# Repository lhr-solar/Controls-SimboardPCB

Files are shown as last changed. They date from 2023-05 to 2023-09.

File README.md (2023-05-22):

# Controls-SimboardPCB

Board's Purpose:

The Controls Sim Board interfaces with the Controls Leader Board in order to simulate the interfacing of the controls system on the car. 

Connections:

LEDs:
* Motor main contactor signal (D1)
* Motor precharge contactor signal (D2)
* Array main contactor signal (D3)
* Array precharge contactor signal  (D4)
Potentiometers:
* Accelerator
* Brake
Switches:
* Ignition
Other:
* CAN connections
* Controls Minion Board passthrough

Mouser BOM:
* Cart link: https://www.mouser.com/ProjectManager/ProjectDetail.aspx?AccessID=63b65d6ddb
* (Spreadsheet of BOM in repo as "Controls-Simboard MouserBom.xls")

Components Outside of Regular Volume:
* 538-43045-1412 (7x2 Molex connector)
* 538-43650-0415 (4x1 Molex connector)
* 538-43045-0612 (3x2 Molex connector)
* 10WA325 (Rotary switch)
* 179-TS16121295260STT (Push button)
* 652-PA45432015CPA503 (Slide Potentiometer)

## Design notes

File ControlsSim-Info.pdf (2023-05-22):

Controls Simboard PCB Information

Full Schematic

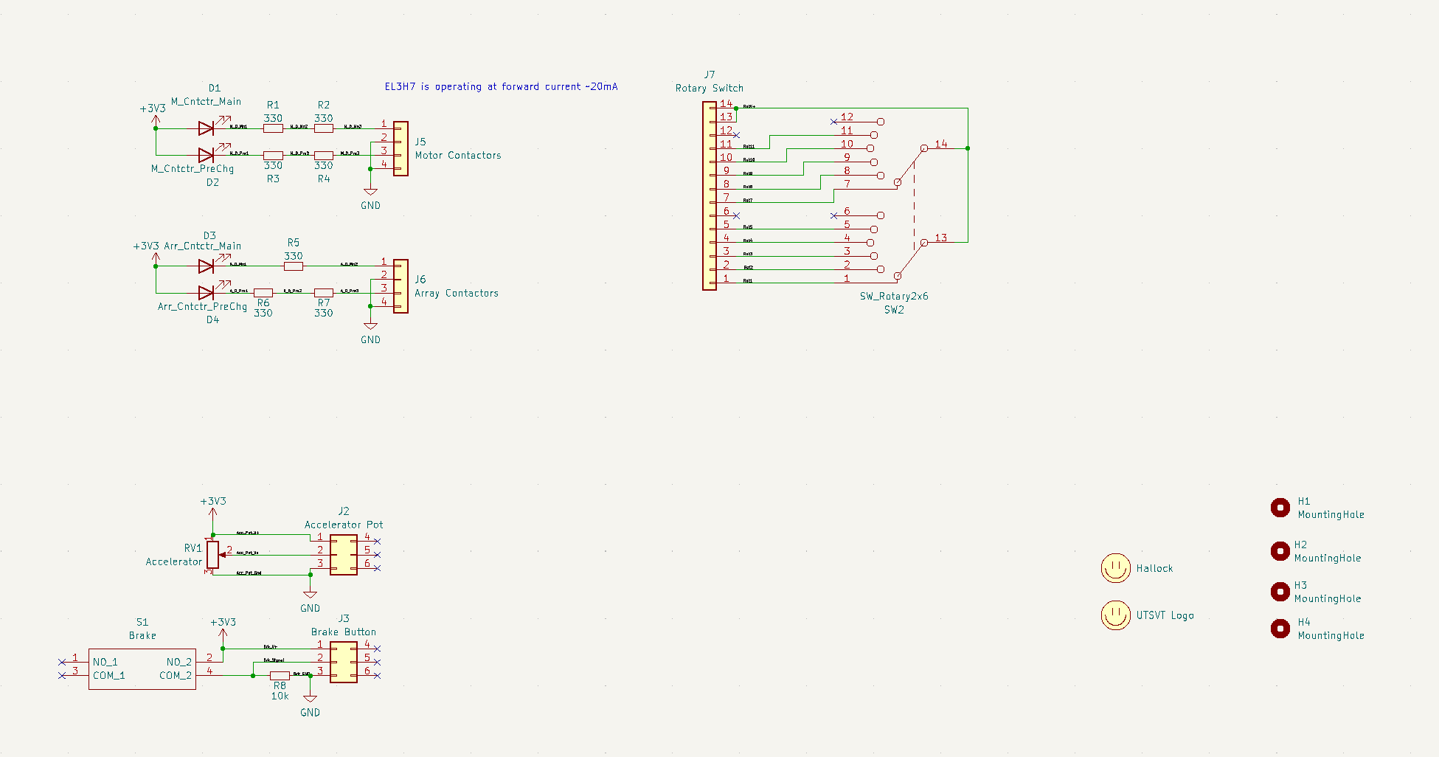
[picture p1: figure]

Board Layout

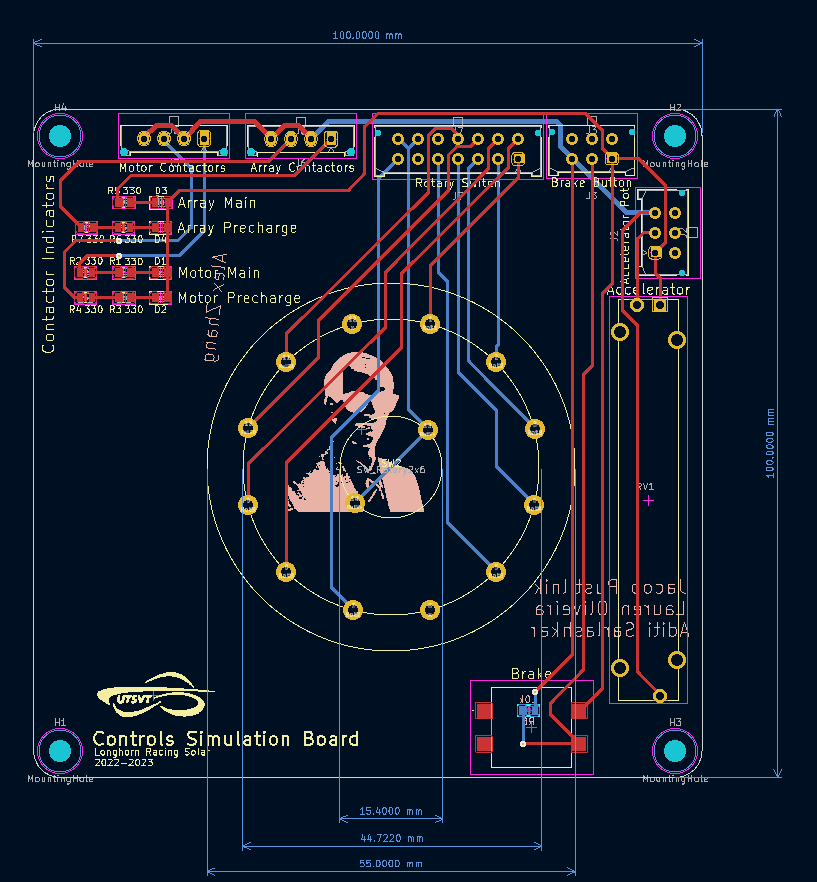
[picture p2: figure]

Board Layout 3D Front

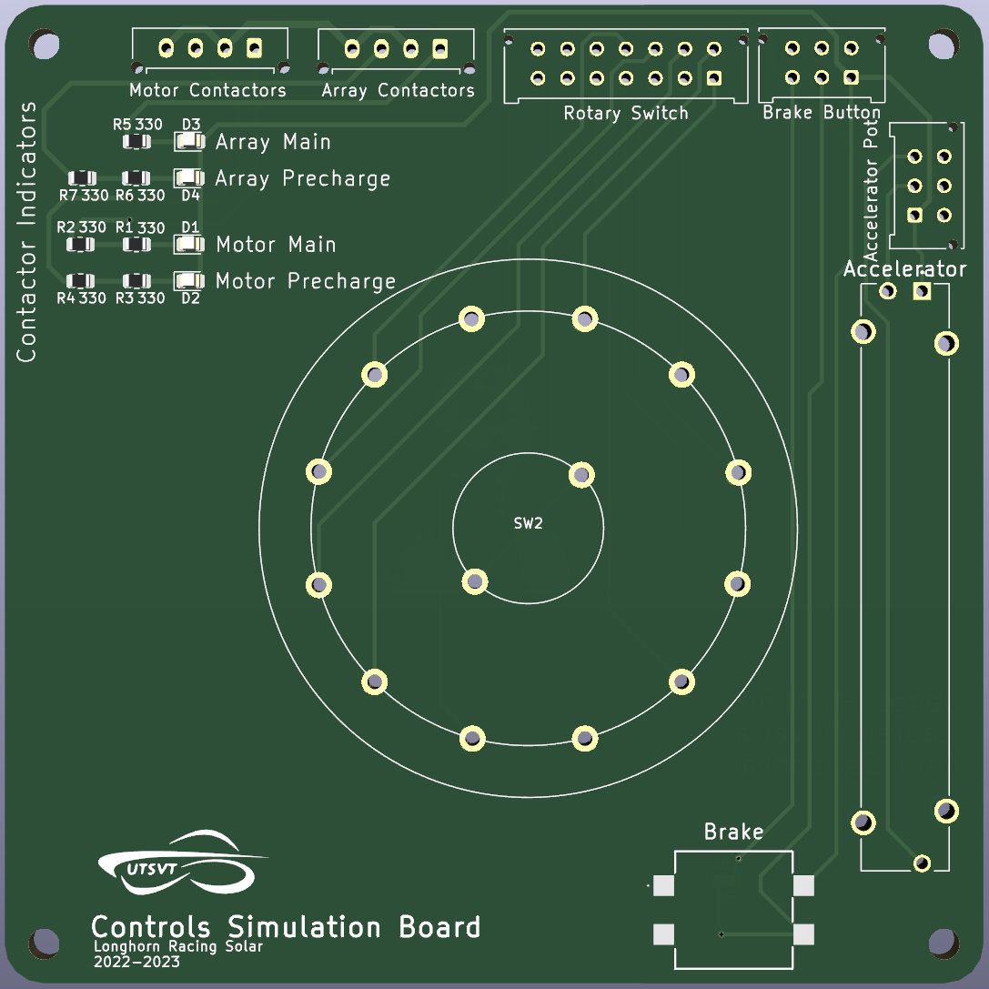
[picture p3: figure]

Board Layout 3D Back

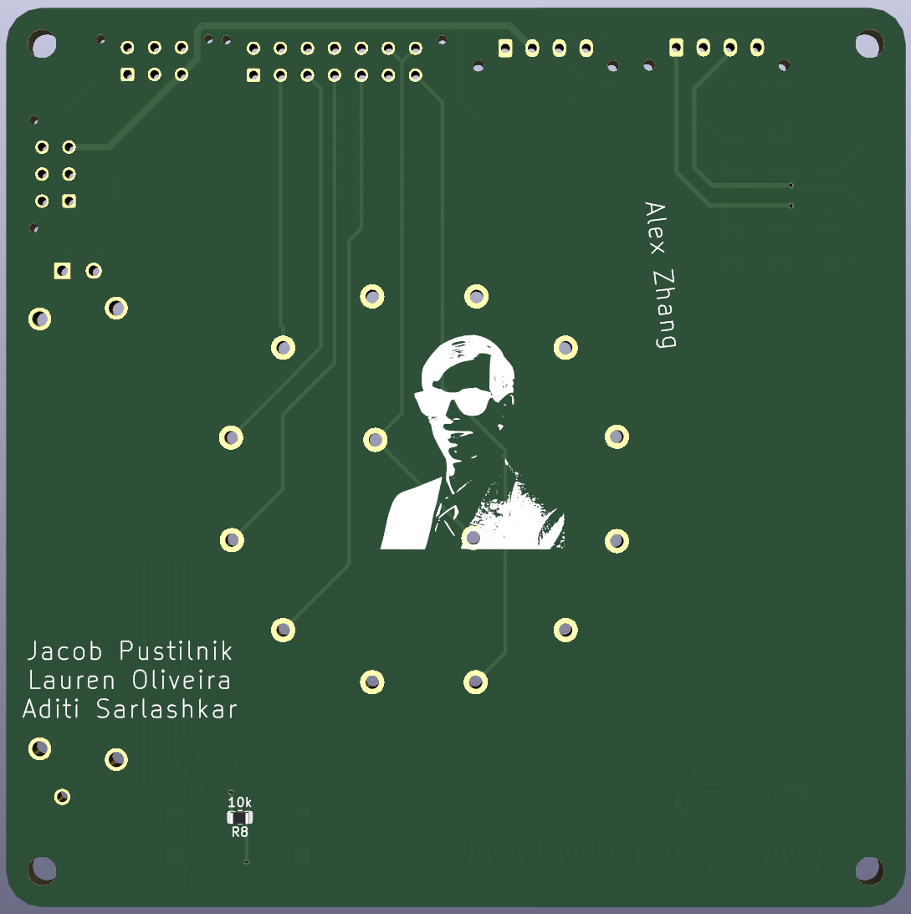
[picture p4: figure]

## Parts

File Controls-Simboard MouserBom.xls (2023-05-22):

Mfr Part Number (Input) | Quantity 1 | Mfr Part Number | Mouser Part Number | Manufacturer Name | Description | Unit Price 1 | Order Quantity | Order Unit Price | Min./Mult. | Availability | Lead Time in Days | Lead Time in Weeks | Lifecycle | NCNR | RoHS | Pb Free | Package Type | Package Quantity | Datasheet URL | Product Image | Design Risk
538-43045-1412 | 1 | 43045-1412 | 538-43045-1412 | Molex | Headers & Wire Housings Headers & Wire Housings 14 CKT VERT HEADER | $3.09 | 1 | $3.09 | 1\1 | 10,056 | 119 | 17 |  | No | Yes | No | TRAY | 936 | https://www.mouser.com/datasheet/2/276/0430451412_PCB_HEADERS-168210.pdf |  | Product has high popularity and is readily available.
10WA325 | 1 | CK1035 | 10WA325 | Lorlin | Rotary Switches Rotary Switches RTRY 2POL 6POS SLDR 6.35X38MM FLAT SHAFT | $7.12 | 1 | $7.12 | 1\1 | 79 | 95 | 14 |  | No | Yes | No | TRAY | 50 | https://www.mouser.com/datasheet/2/242/CK_Datasheet_Mar_2020-1890608.pdf |  | Product has high popularity and is readily available.
538-43650-0415 | 2 | 43650-0415 | 538-43650-0415 | Molex | Headers & Wire Housings Headers & Wire Housings VERT SMT PCB HDR 4P sngl polarizing pins | $1.19 | 2 | $1.19 | 1\1 | 18,797 | 77 | 11 |  | No | Yes | Yes | TRAY | 120 | https://www.mouser.com/datasheet/2/276/0436500415_PCB_HEADERS-148705.pdf |  | Product has high popularity and is readily available.
538-43045-0612 | 2 | 43045-0612 | 538-43045-0612 | Molex | Headers & Wire Housings Headers & Wire Housings 6 CKT VERT HEADER | $0.67 | 2 | $0.67 | 1\1 | 12,341 | 119 | 17 |  | No | Yes | No | TRAY | 144 | https://www.mouser.com/datasheet/2/276/3/0430450612_PCB_HEADERS-2877224.pdf |  | Product has high popularity and is readily available.
179-TS16121295260STT | 1 | TS16-1212-95-BK-260-SMT-TR | 179-TS16121295260STT | CUI Devices | Tactile Switches Tactile Switches 12 x 12 mm 9.5 mm Actuactor Height 260gf Black Surface Mount TR SPST | $0.38 | 1 | $0.38 | 1\1 | 1,877 | 21 | 3 | New Product | No | Yes | No |  | 400 | https://www.mouser.com/datasheet/2/670/ts16-2944012.pdf |  | Product is new and is readily available.
71-CRCW080510K0FKEAC | 1 | CRCW080510K0FKEAC | 71-CRCW080510K0FKEAC | Vishay | Thick Film Resistors - SMD Thick Film Resistors - SMD 1/8Watt 10Kohms 1% Commercial Use | $0.10 | 1 | $0.10 | 1\1 | 1,149,420 | 191 | 28 |  | No | Yes | No | REEL | 5,000 | https://www.vishay.com/doc?28773 |  | Product has high popularity and is readily available.
71-CRCW0805330RJNEAC | 7 | CRCW0805330RJNEAC | 71-CRCW0805330RJNEAC | Vishay | Thick Film Resistors - SMD Thick Film Resistors - SMD 1/8Watt 330ohms 5% Commercial Use | $0.10 | 7 | $0.10 | 1\1 | 60,251 | 174 | 25 |  | No | Yes | No | REEL | 5,000 | https://www.vishay.com/doc?28773 |  | Product has high popularity and is readily available.
604-APTD2012LCGCK | 4 | APTD2012LCGCK | 604-APTD2012LCGCK | Kingbright | Standard LEDs - SMD Standard LEDs - SMD 0805 Dome Lens LED Green- 570nm | $0.40 | 4 | $0.40 | 1\1 | 36,893 | 56 | 8 |  | No | Yes | Yes | REEL | 3,000 | https://www.mouser.com/datasheet/2/216/APTD2012LCGCK-1102037.pdf |  | Product has high popularity and is readily available.
652-PA45432015CPA503 | 1 | PTA4543-2015CPA503 | 652-PA45432015CPA503 | Bourns | Slide Potentiometers Slide Potentiometers PANEL CONTROL - SLIDE CARBON | $2.07 | 1 | $2.07 | 1\1 | 490 | 140 | 20 |  | No | Yes | No | TRAY | 100 | https://www.mouser.com/datasheet/2/54/pta-778345.pdf |  | Product has high popularity and is readily available.

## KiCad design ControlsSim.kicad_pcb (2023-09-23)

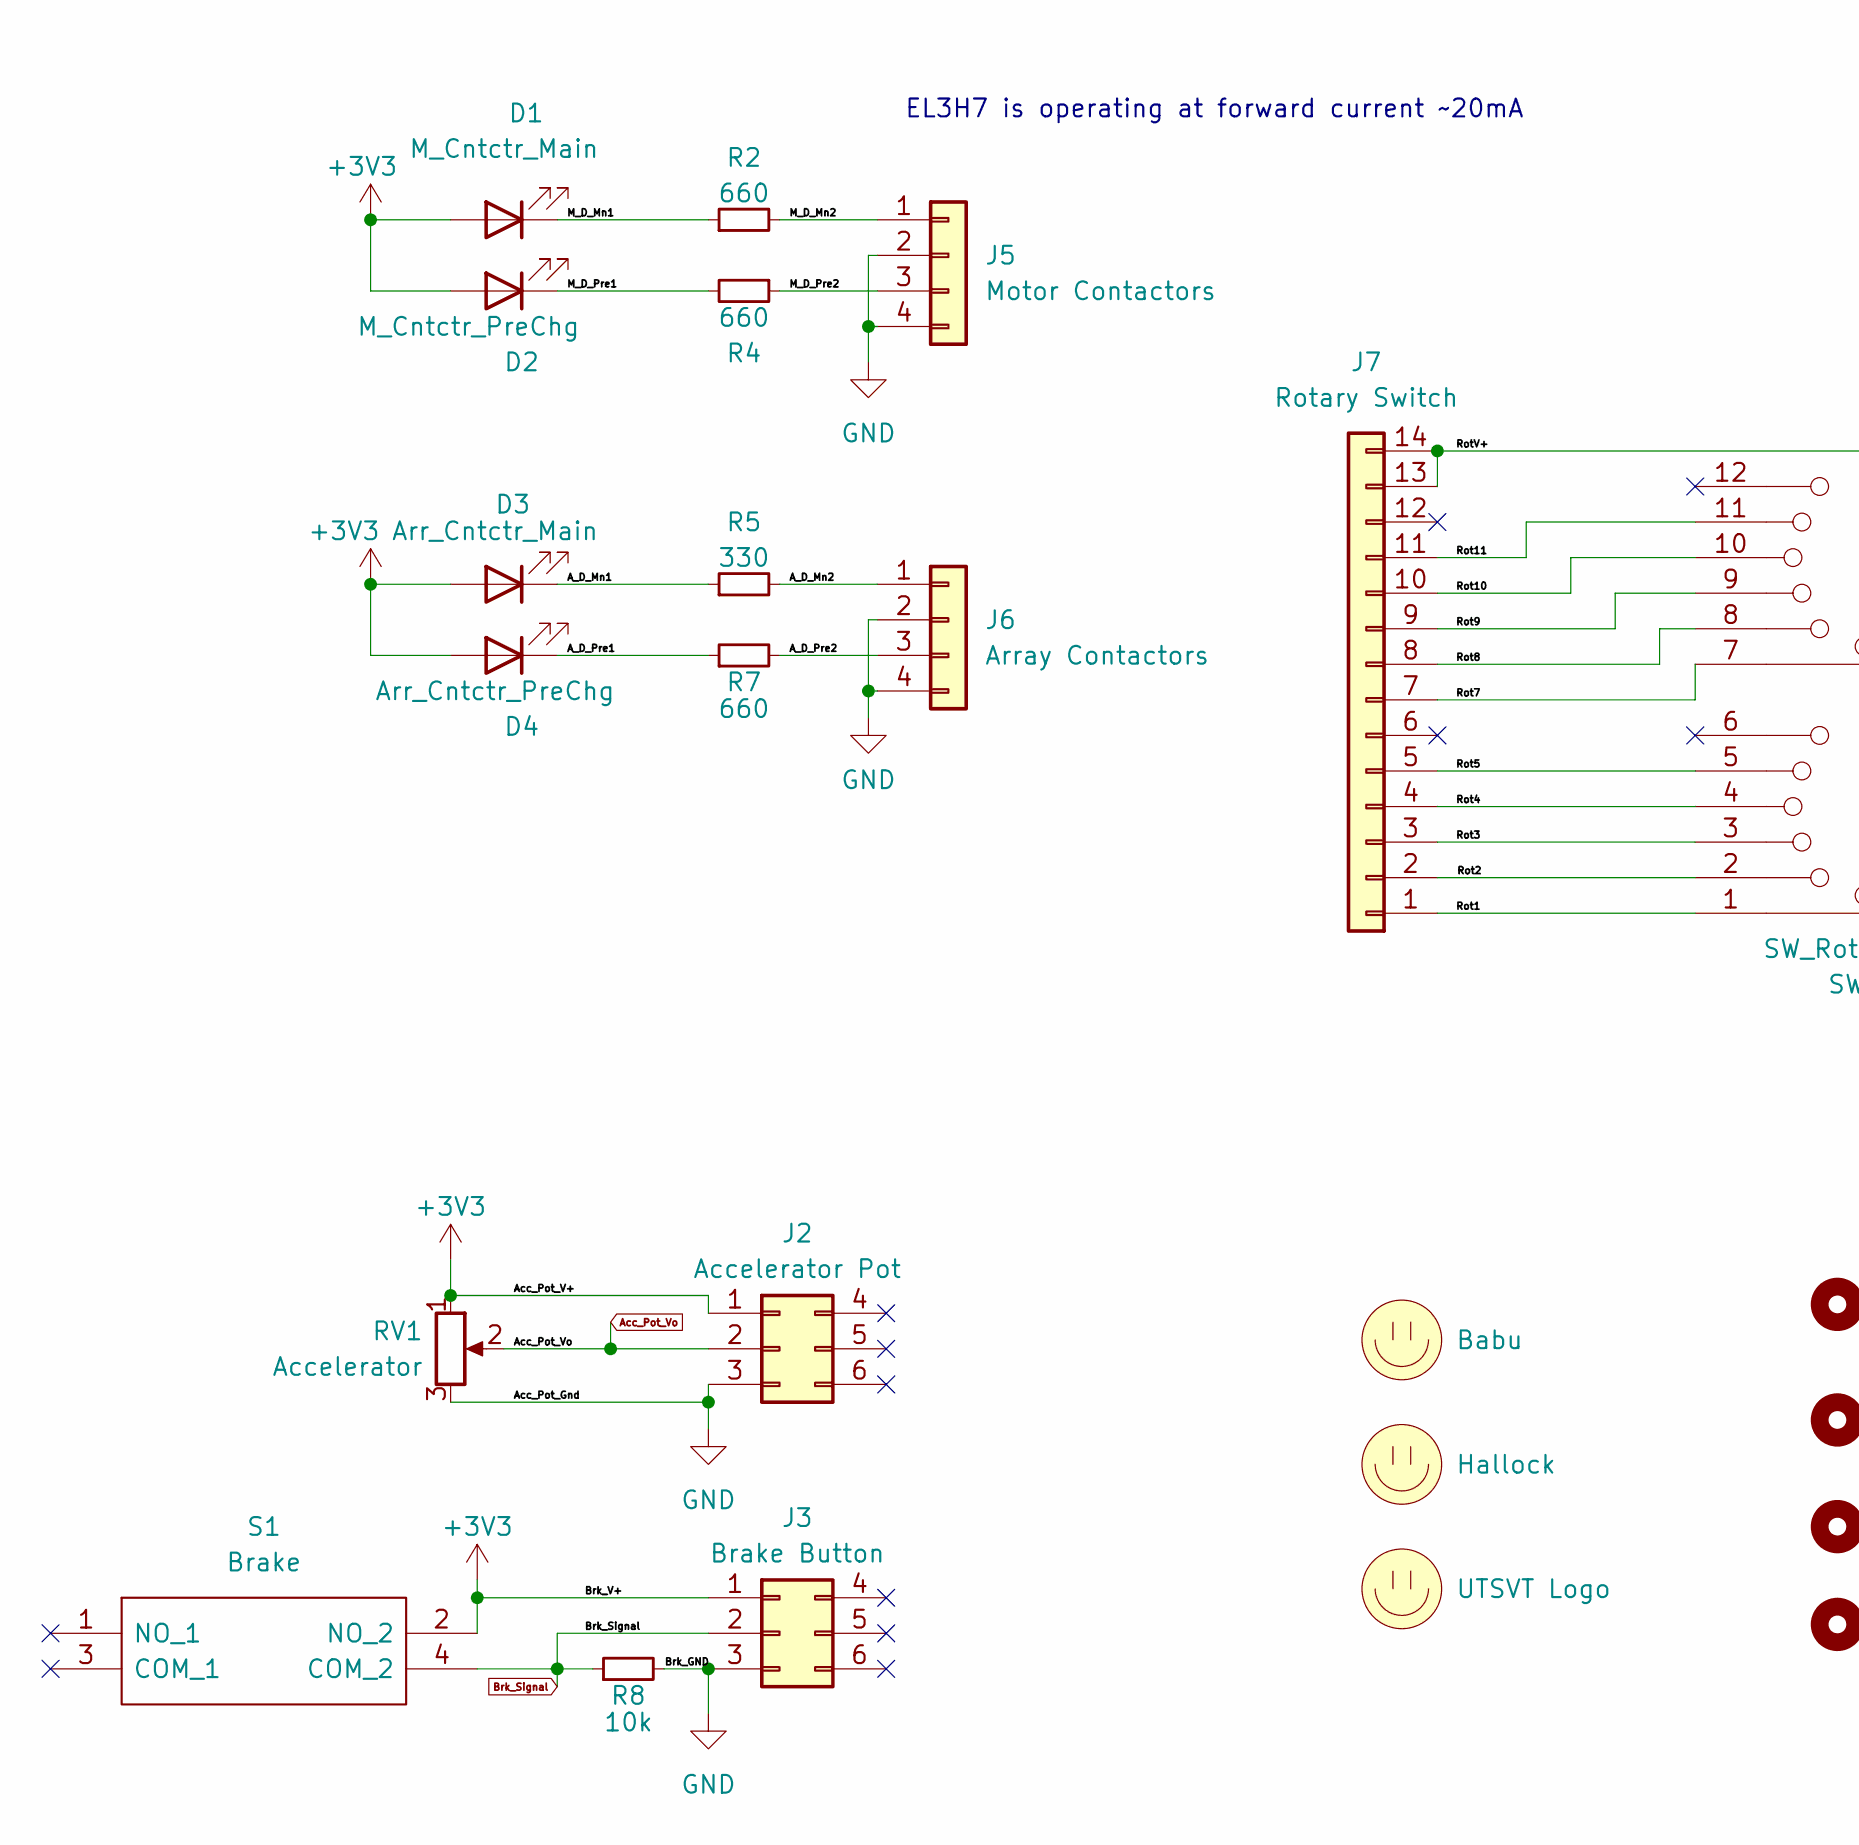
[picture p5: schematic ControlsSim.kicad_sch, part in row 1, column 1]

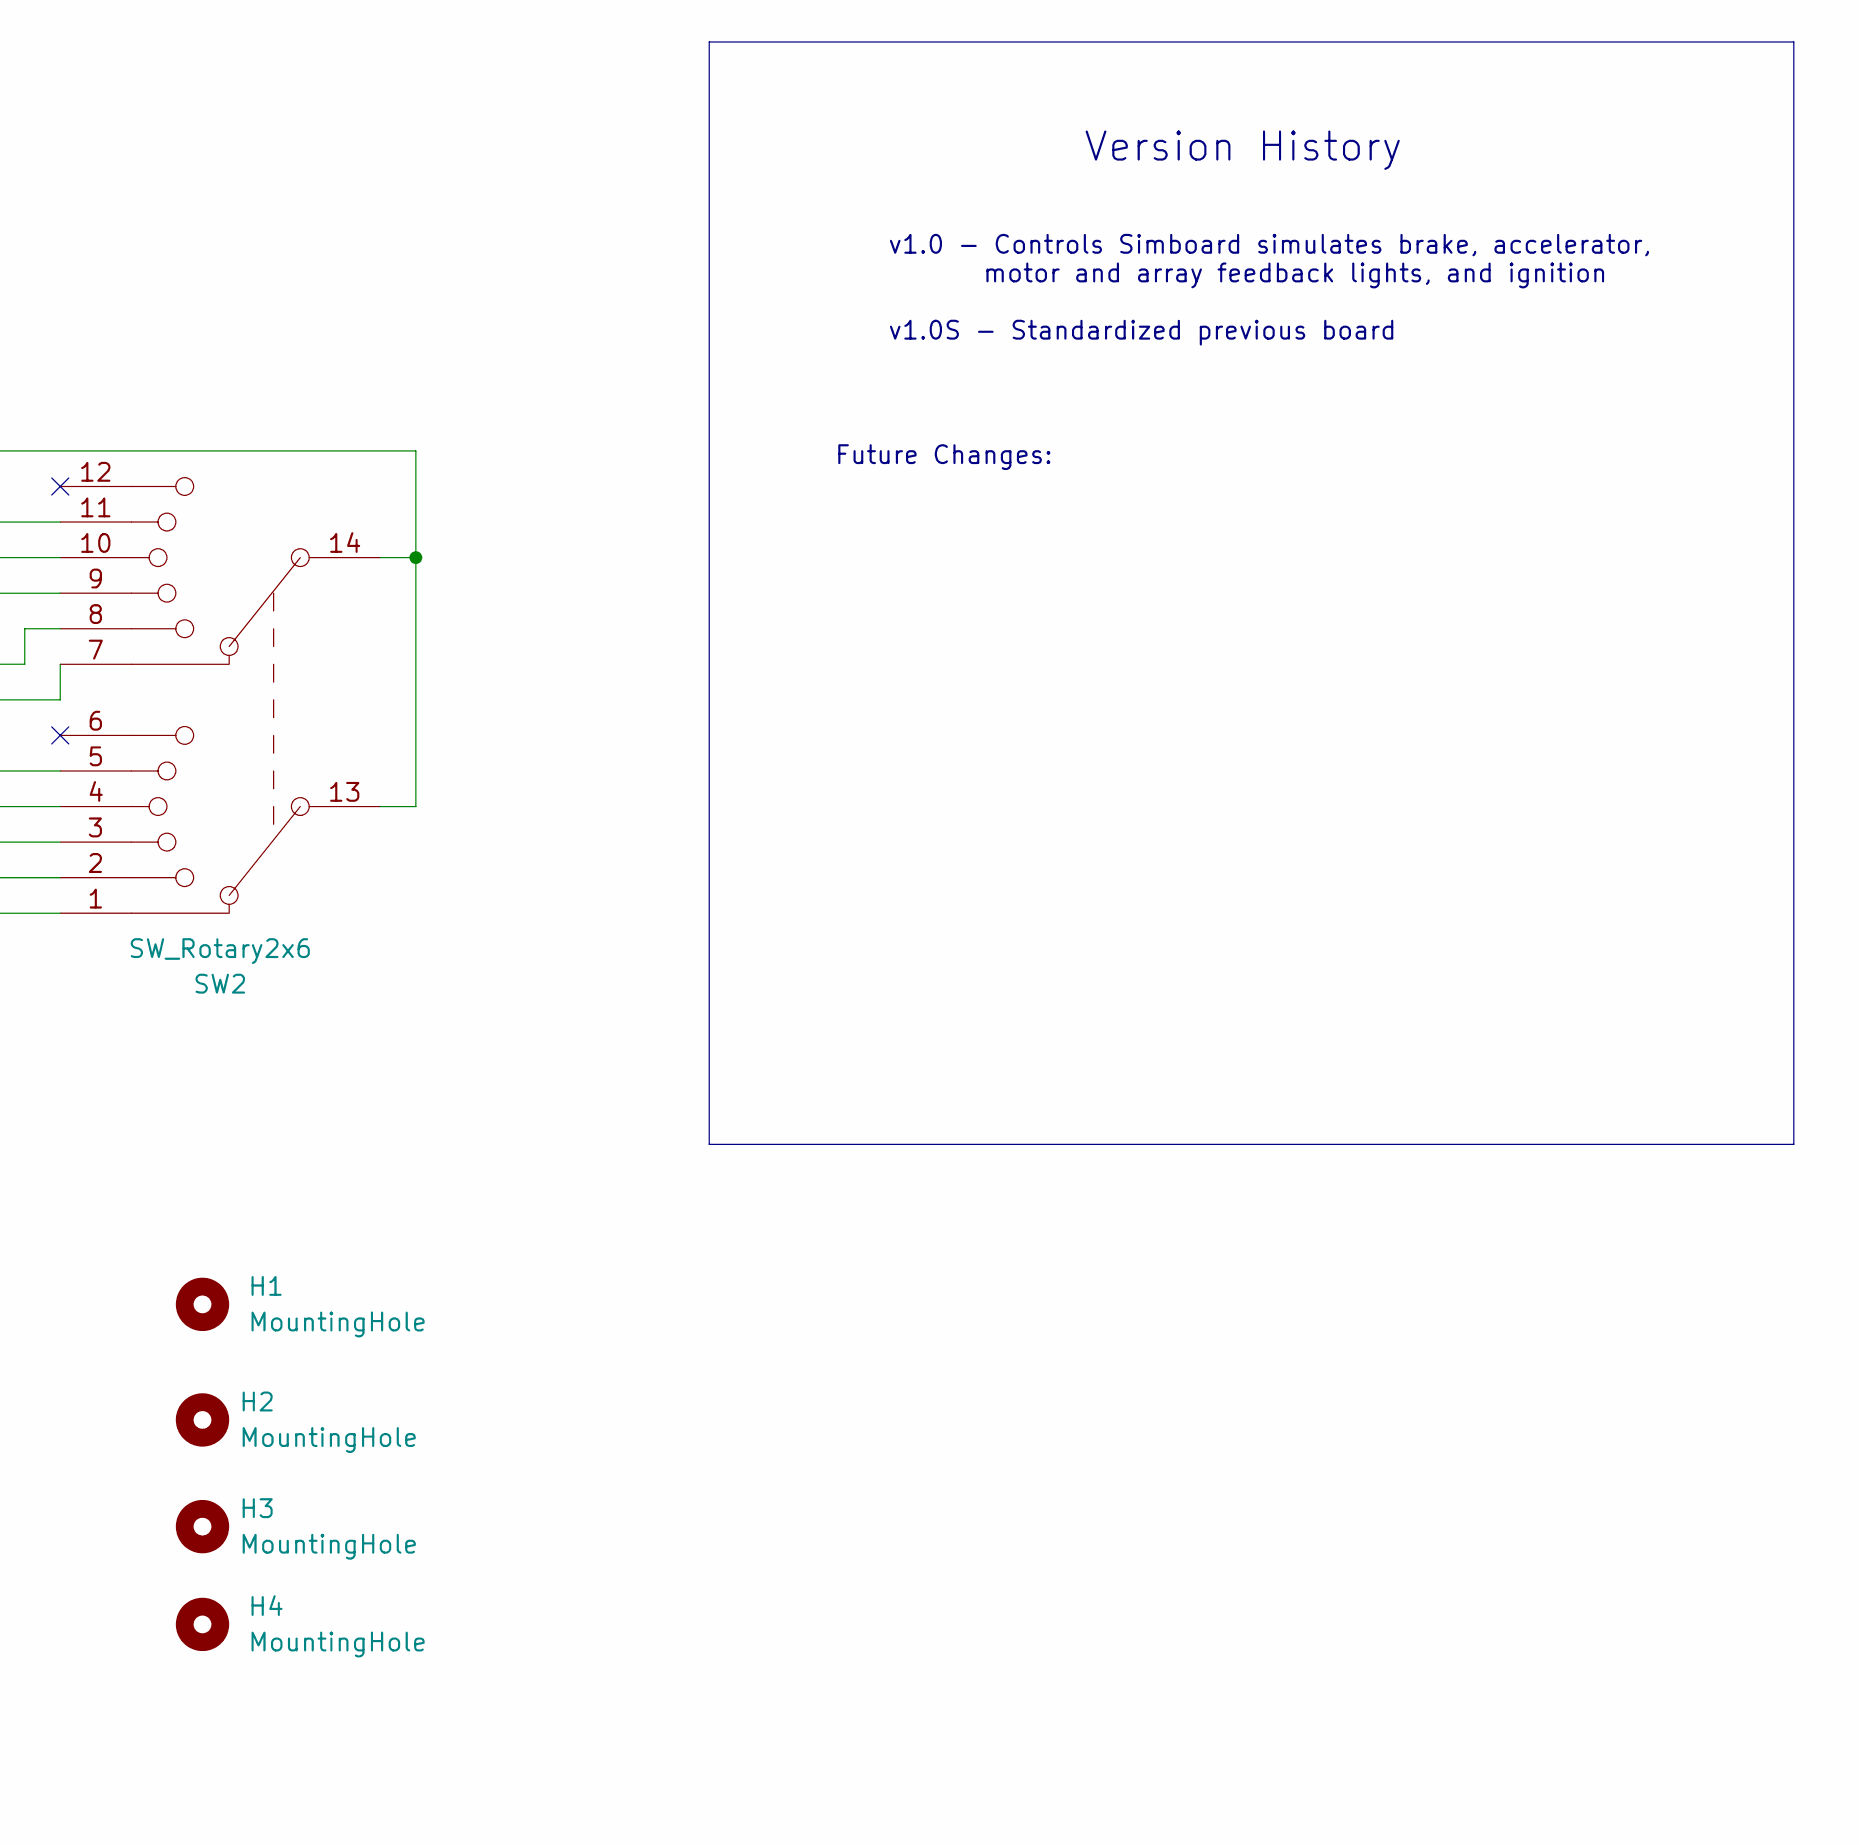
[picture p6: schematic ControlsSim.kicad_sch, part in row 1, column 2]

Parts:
D1: M_Cntctr_Main; LED_0805_2012Metric; MFG PN APTD2012LSYCK
D2: M_Cntctr_PreChg; LED_0805_2012Metric; MFG PN APTD2012LSURCK
D3: Arr_Cntctr_Main; LED_0805_2012Metric; MFG PN APTD2012LVBC/D
D4: Arr_Cntctr_PreChg; LED_0805_2012Metric; MFG PN APTD2012LCGCK
H1, H2, H3, H4: MountingHole; MountingHole_3.2mm_M3
J2: Accelerator Pot; Molex_Micro-Fit_3.0_43045-0612_2x03_P3.00mm_Vertical
J3: Brake Button; Molex_Micro-Fit_3.0_43045-0612_2x03_P3.00mm_Vertical
J5: Motor Contactors; Molex_Micro-Fit_3.0_43650-0415_1x04_P3.00mm_Vertical
J6: Array Contactors; Molex_Micro-Fit_3.0_43650-0415_1x04_P3.00mm_Vertical
J7: Rotary Switch; Molex_Micro-Fit_3.0_43045-1412_2x07_P3.00mm_Vertical
LOGO1: Hallock; Hallock_Image_Small
LOGO2: UTSVT Logo; UTSVT_Logo_Symbol
LOGO3: Babu; Babu the Builder
R2, R4, R7: 660; R_0805_2012Metric
R5: 330; R_0805_2012Metric
R8: 10k; R_0805_2012Metric; Mfg PN CRCW080510K0FKEAC
RV1: Accelerator; PTA4543
S1: Brake; TS16121295BK260SMTTR; Manufacturer_Part_Number TS16-1212-95-BK-260-SMT-TR
SW2: SW_Rotary2x6; CK1035_resized

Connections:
+3V3: D1.2 (A), D2.2 (A), D3.2 (A), D4.2 (A), J2.1, J3.1, RV1.1, S1.2 (NO_2)
/A_D_Mn1: D3.1 (K), R5.1
/A_D_Mn2: J6.1, R5.2
/A_D_Pre1: D4.1 (K), R7.1
/A_D_Pre2: J6.3, R7.2
/M_D_Mn1: D1.1 (K), R2.1
/M_D_Mn2: J5.1, R2.2
/M_D_Pre1: D2.1 (K), R4.2
/M_D_Pre2: J5.3, R4.1
/Rot1: J7.1, SW2.1
/Rot2: J7.2, SW2.2
/Rot3: J7.3, SW2.3
/Rot4: J7.4, SW2.4
/Rot5: J7.5, SW2.5
/Rot7: J7.7, SW2.7
/Rot8: J7.8, SW2.8
/Rot9: J7.9, SW2.9
/Rot10: J7.10, SW2.10
/Rot11: J7.11, SW2.11
/RotV+: J7.13, J7.14, SW2.13, SW2.14
Acc_Pot_Vo: J2.2, RV1.2
Brk_Signal: J3.2, R8.1, S1.4 (COM_2)
GND: J2.3, J3.3, J5.2, J5.4, J6.2, J6.4, R8.2, RV1.3

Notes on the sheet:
v1.0 - Controls Simboard simulates brake, accelerator, motor and array feedback lights, and ignition v1.0S - Standardized previous board
Future Changes:
EL3H7 is operating at forward current ~20mA
Version History

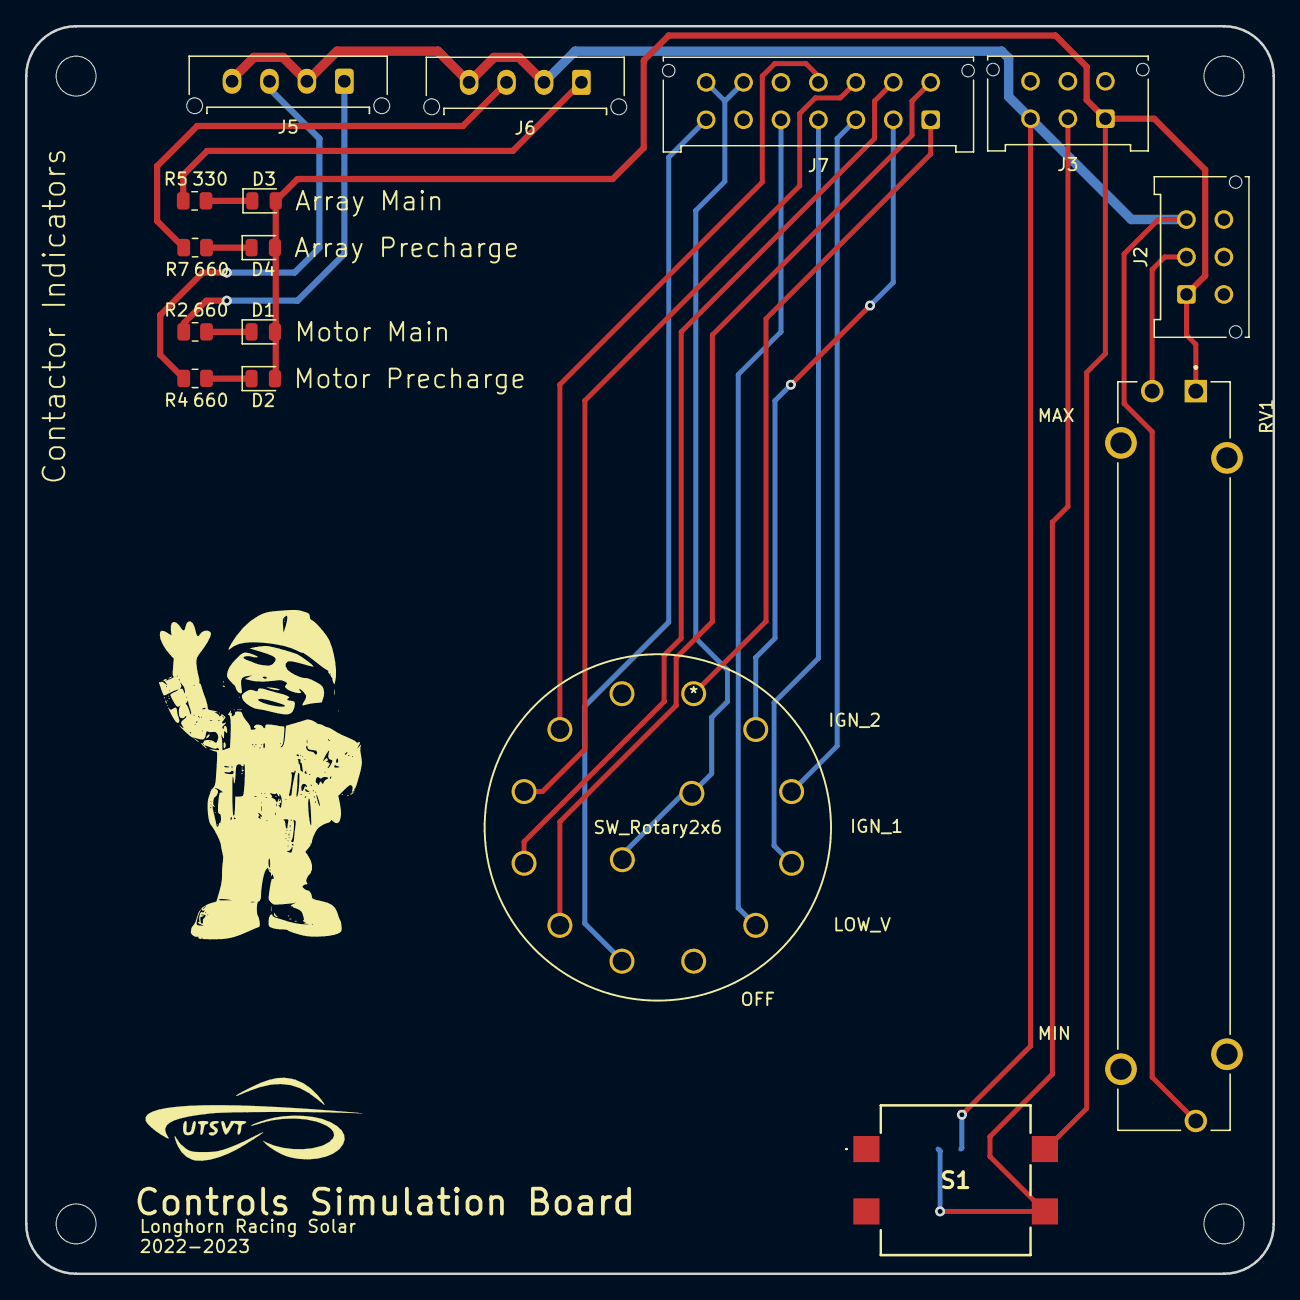
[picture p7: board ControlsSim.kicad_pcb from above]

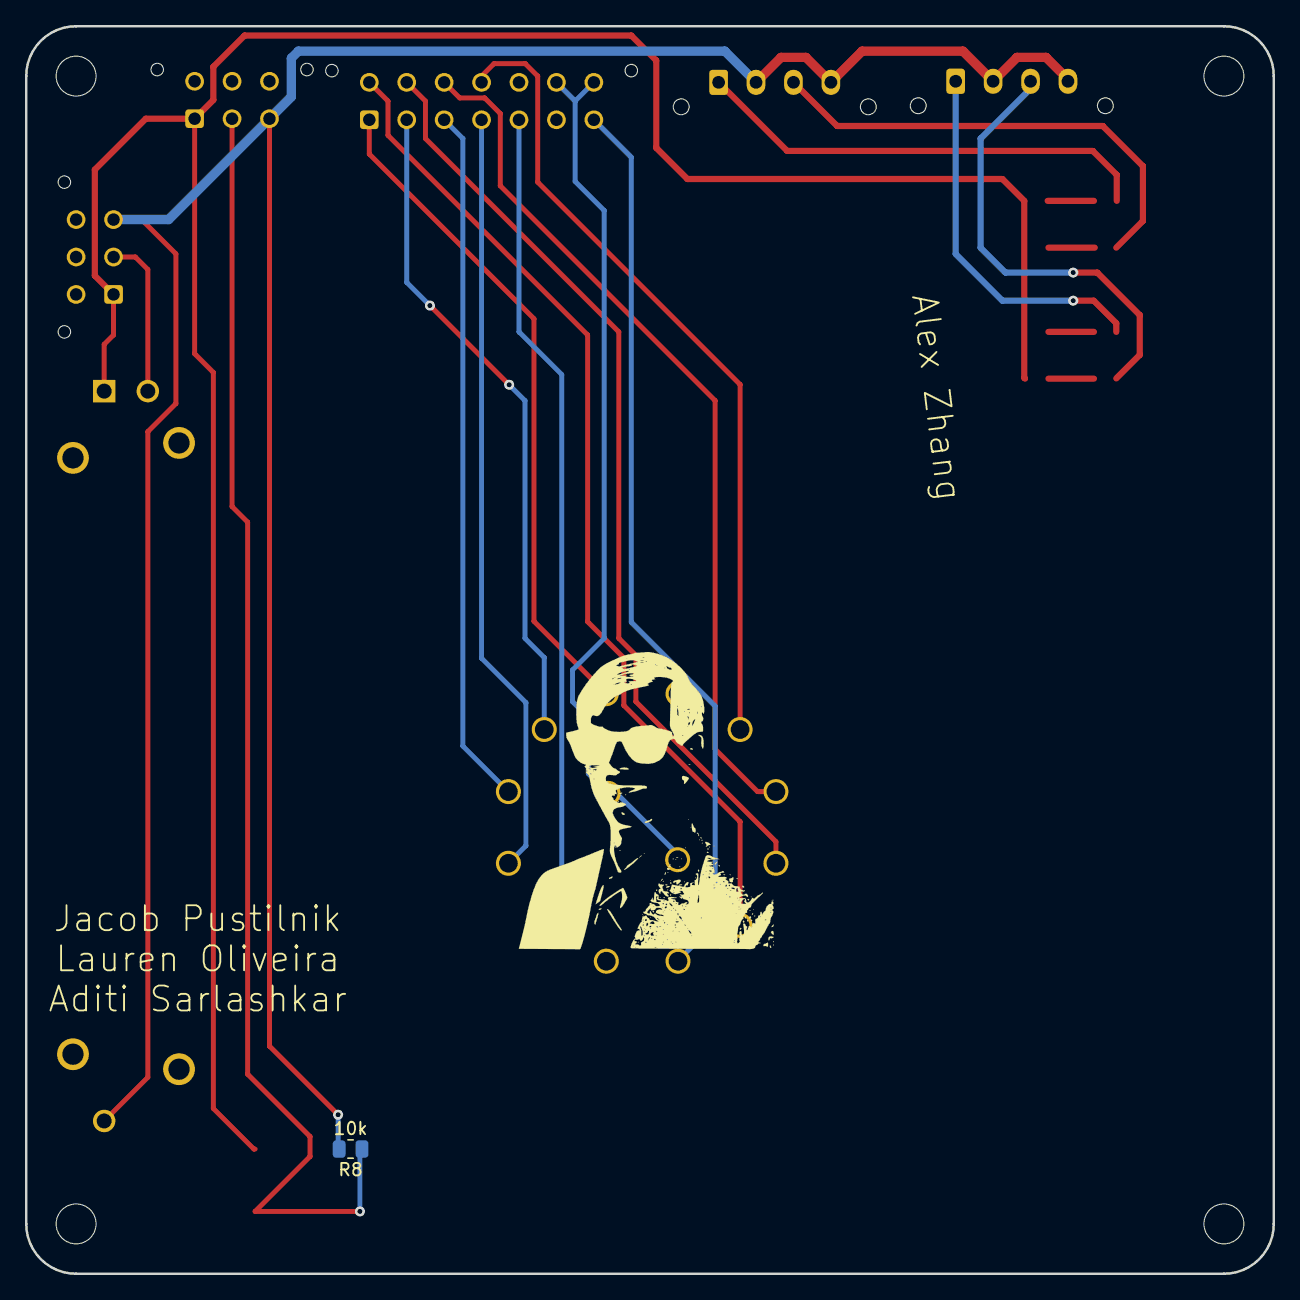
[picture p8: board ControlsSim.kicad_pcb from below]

Board: 2 copper layers, 100.0 x 100.0 mm, 24 parts (2 on the bottom side), 23 nets.

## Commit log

2022-09-24 Adds pcb parts library
2022-09-24 Empty KiCad file
    [Controls-SimboardPCB.kicad_pcb, Controls-SimboardPCB.kicad_sch, ControlsSimboard.kicad_pcb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]
2022-10-01 Blank KiCad file and branch creation
    [ControlsSim.kicad_pcb, ControlsSim.kicad_sch]
2022-10-22 Initial schematic with parts
    [Controls-SimboardPCB.kicad_pcb, Controls-SimboardPCB.kicad_sch, ControlsSim.kicad_sch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]
2022-10-29 Revised schematic with input from Babu, intial PCB layout
    [ControlsSim.kicad_pcb, ControlsSim.kicad_sch]
2022-11-12 almost final PCB
    [ControlsSim.kicad_pcb, ControlsSim.kicad_sch]
2022-11-12 added logos
    [ControlsSim.kicad_pcb, ControlsSim.kicad_sch]
2022-12-03 removed display connector
    [ControlsSim.kicad_pcb, ControlsSim.kicad_sch]
2022-12-03 minor silkscreen text movement
    [ControlsSim.kicad_pcb]
2022-12-03 shortened traces of contactor LEDs, moved upward
    [ControlsSim.kicad_pcb]
2023-01-12 Changed LED colors to use all four colors, one for each contactor
    [ControlsSim.kicad_pcb, ControlsSim.kicad_sch]
2023-02-04 Generated gerbers and drill files
    [ControlsSim-B_Cu.gbr, ControlsSim-B_Mask.gbr, ControlsSim-B_Paste.gbr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]
2023-02-05 Added zip file of gerbers
2023-05-22 Beginning of Standardization
    [ControlsSim.kicad_pcb]
2023-05-22 README and BOM Finished
    Updated the README according to new guidelines and added the BOM spreadsheet as a .xls
    [Controls-Simboard MouserBom.xls]
2023-05-25 Added Missing Datasheets
    [ControlsSim.kicad_sch]
2023-05-25 Fixed DRC
    [ControlsSim.kicad_pcb]
2023-05-28 Fixed Submodule, added Version History, and fixed folder organization
    [ControlsSim-B_Cu.gbr, ControlsSim-B_Mask.gbr, ControlsSim-B_Paste.gbr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]
2023-05-29 KiCad 7.0
    [ControlsSim.kicad_pcb, ControlsSim.kicad_sch]
2023-06-14 Updated version history and implemented a fix for 3dmodels to be applied next commit
    [ControlsSim.kicad_sch]
2023-06-19 Fixed directories for footprints and 3D models, also fixed incorrect footprint and 3d model for rotary encoder.
    [ControlsSim.kicad_pcb]
2023-08-26 Fixed DRC issue and removed extraneous traces
    [ControlsSim.kicad_pcb, ControlsSim.kicad_sch]
2023-09-23 Updated silkscreen that Controls wanted
    [ControlsSim.kicad_pcb]
2023-09-23 Fixed resistor value and layout, fixed labels for rotary encoder.
    [ControlsSim.kicad_pcb, ControlsSim.kicad_sch]
2023-09-23 Updated ibom and gerbers
    [ControlsSim-B_Cu.gbr, ControlsSim-B_Mask.gbr, ControlsSim-B_Paste.gbr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]
2023-09-23 fixed ibom
    [ControlsSim-NPTH.drl, ControlsSim-PTH.drl]

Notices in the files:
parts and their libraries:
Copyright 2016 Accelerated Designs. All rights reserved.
